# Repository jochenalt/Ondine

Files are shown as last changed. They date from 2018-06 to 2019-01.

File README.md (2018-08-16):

# Ondine
Ondine is a lovely ballet of robots. Right in the middle of development. Check the [Documentation](http://ondine.readthedocs.io). Contact me via the [hackaday page](https://hackaday.io/post/53678).

work in progress

### Contents
    /cad 	    CAD designs in Inventor 2018
    /theory     mainly on kinematics
    /code       source code (mainly C++)
    /schematics schematics in EAGLE 
    /docs		source of Ondine's [Documentation](https://http://ondine.readthedocs.io)
    /datasheets datasheets of components Ondine is made of

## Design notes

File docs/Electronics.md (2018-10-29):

# Electronics

Electronics takes care of the following topics

* <b>Control of the three brushless motors</b>. Brushless motoros require more control and electronics than brushed motors. Since industrial controlers are quite expensive, I did my own based on the [L6234 three phase motor driver](https://www.st.com/content/ccc/resource/technical/document/application_note/78/44/47/d5/a8/63/4a/8e/CD00004062.pdf/files/CD00004062.pdf/jcr:content/translations/en.C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), which is kind of outdated, but still has nice specs.
* <b>Running Kinematics and state control</b>. Kinematics and state control need to run with a high frequency and reasonable precision. I went with a [Teensy 3.5](https://www.pjrc.com/store/teensy35.html) ARM controller with 120MHz providing floating point arithmetics in hardware.
* <b>Communicate with the outside world</b>. The bot communicates via a small webserver connected to a local Wifi using the popular [ESP8266](https://www.seeedstudio.com/NodeMCU-v2-Lua-based-ESP8266-development-kit-p-2415.html) device.

# Control of a Brushless Motor

A brushless motor is driven by a magnetic field that turns 90° in advance of the motor's rotor. The diagram shows how this works in general.

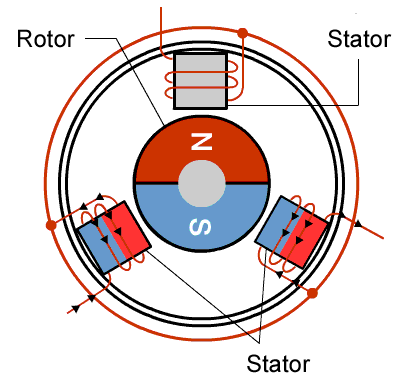
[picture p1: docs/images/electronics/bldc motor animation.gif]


But, the magnetic field turns in jumps of 120° which leads to high vibrations and jerky rotation especially when working at low speed. To improve that, the magnetic field has to turn continuously, which we can achieve by applying three sin waves modulated by PWM to each stator resulting in a smoothly turning magnetic field.

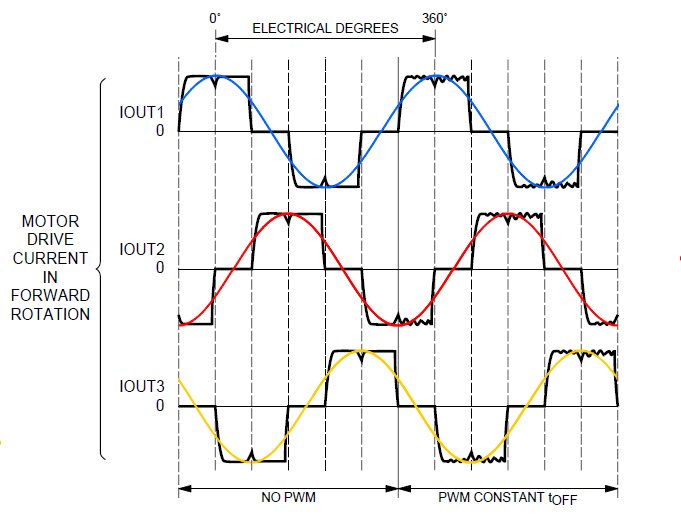
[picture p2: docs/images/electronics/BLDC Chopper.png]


To improve the ripple of the movement, space vector PWM (SVPM) can be used instead of plain PWM modulating sine waves. This is kind of electrical engineering black magic, an introduction can be found [here](https://www.switchcraft.org/learning/2017/3/15/space-vector-pwm-intro), frankly I did not spend the effort to dig into it, since it is so easy to implement and gains you a smoother movement.

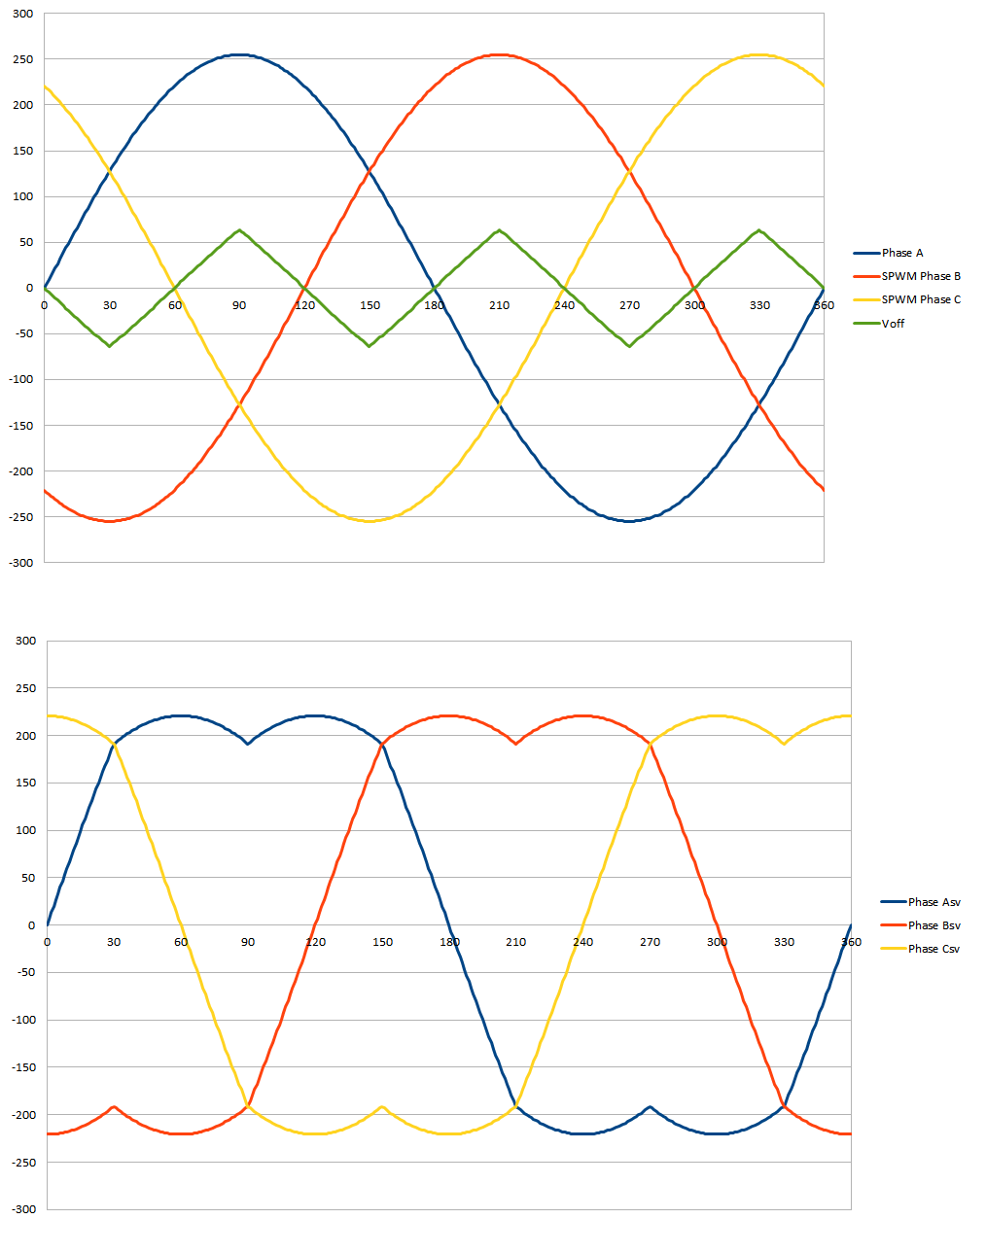
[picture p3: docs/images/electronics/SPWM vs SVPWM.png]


Computation is done by 





The motor driver L6234 has three PWM inputs, which need to be fed with svpm(t), svpwm (t + 120°), and svpwm(t + 240°). 

## Initial Calibration

The initial position of the rotor has to be considered in order to drive the magnetic field 90° ahead of the rotor's positon. For this purpose, I use an optical encoder with a startup procedure identifying the initial angle of the rotor (later on, it came to my mind that an absolute magnetic encoder could do this without the startup procedure. But it was too late).

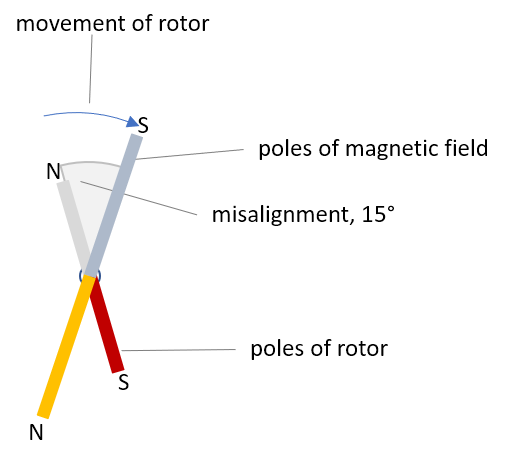
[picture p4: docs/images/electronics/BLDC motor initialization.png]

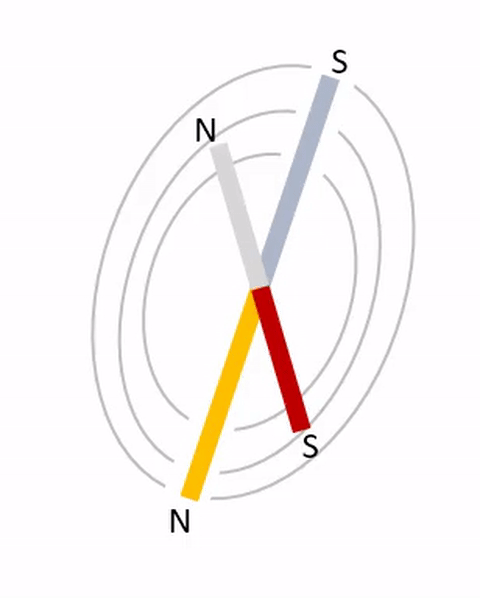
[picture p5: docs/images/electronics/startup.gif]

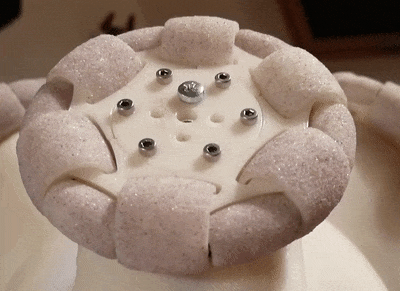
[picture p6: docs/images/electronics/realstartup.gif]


After the initialization procedure we know the current angle of the rotor. It is used later on to turn the magnetic field 90° ahead of the rotor. When we switch on the motor, we start with a very little amount of torque. The torque is slowly increased until the encoder recognized a movement. This happens after approx 0.3° (I have 1024 CPR encoders). The direction of the movement indicates the direction of the rotor's position relatively to the magnetic field. Now the magnetic field is turned torwards the rotor until the rotor has reached its starting position. We slightly increase the torque and start again waiting for a small movement which is then compensatd by turning the magnetic field. We repeat that until the magnetic field is perfectly aligned with the rotor while applying maximum torque. 

By this procdure, the magnetic files turns towards the current position of the rotor with increasing verve. It takes approx. 1s and is recognizable by a very small and short osccillation when starting up.

The advance angle of 90 degrees implies an issue when doing position control: If the motor is supposed to stick at one position and there's varying torque, the advance angle jumps from +90° to -90° everytime the control algrithm changes its direction. To avoid that jump, the PID controller's output is smoothed by a sigmoid function:



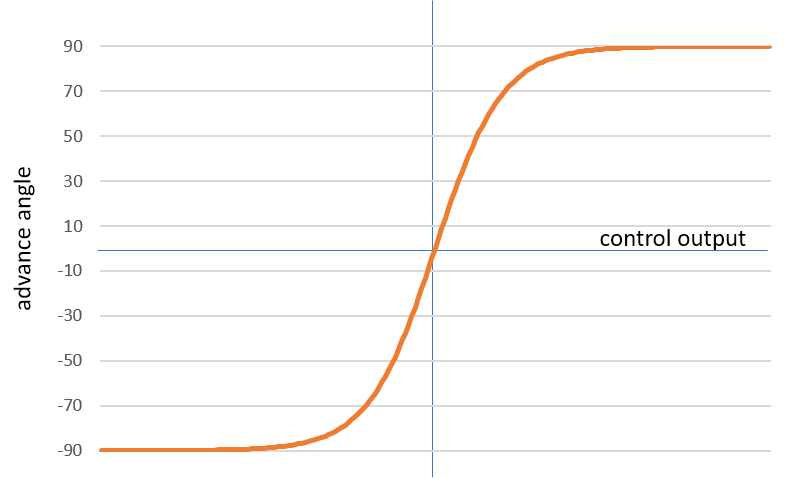
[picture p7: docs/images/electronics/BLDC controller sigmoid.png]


## PID Controller

Speaking of the PID controller of a brushless motor : I played around with a couple of controllertypes, I even implemented one of these fancy fuzzy controllers. Did not work out well, actually I got the impression that fuzzy controllers are kind of an academic hype only. I ended up with a plain gain-scheduled PID controller, i.e. a PID controller that has two sets of PID values: One for balancing, one for maximum speed. The input speed is used to identify the gains by interpolation between these two configuration sets.

All this is implemented in [BrushlessMotorDriver.cpp](https://github.com/jochenalt/Ondine/blob/master/code/BotController/BrushlessMotorDriver.cpp).

# Communication

The device should communicate with the outside world. A fully fledged SOC board (Raspberry or ODroid) seemed to be an overkill, so I used a small web module that became famous a couple of years ago. The [ESP8266](https://www.seeedstudio.com/NodeMCU-v2-Lua-based-ESP8266-development-kit-p-2415.html) can be programmed in C++ in an Eclipse IDE and already has a library implementing a webserver. Those weired scripting languages that always come with a device like that (in this case "LUA"), is nothing I wanted to spend time with.



# Microcontroller

The microcontroller should run the state control to make the bot balance and move, it has to control the motor drivers which uses up some capacity, and it has to receive commands coming from the webserver module. An Avr uC would be too much of a tuning pain, a fully fledged Linux board would be overengineered, so I went with my favrourite controller, a [Teensy 3.5](https://www.pjrc.com/store/teensy35.html) that has a 32bit-Arm M4 controller with enough memory, 120MHz, 5V compatibility, and a 32-bit FPU which comes in handy for kinematics and state control.



# Schematics 

The motors pull 2A max, so I choose the [L6234](https://www.st.com/content/ccc/resource/technical/document/application_note/78/44/47/d5/a8/63/4a/8e/CD00004062.pdf/files/CD00004062.pdf/jcr:content/translations/en.C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) to avoid soldering 18 MOSFETs. Luckily, there's a nice breakout from [Drotek](https://drotek.com/shop/en/home/212-brushless-gimbal-controller-l6234.html) that is convinient to use.

[](https://drotek.com/shop/505-large_default/brushless-gimbal-controller-l6234.jpg)

On the IMU side I went with the cheap and reliable MPU9250 on a drotek breakout

[](https://drotek.com/shop/en/imu/421-mpu9250-gyro-accelerometer-magnetometer.html)

There's not a big deal in the schematics, pretty standard I would say. There's a power supply with a switching 7805 (D3) (a normal power regulator would have required a heatsink for which I dont have enough space on the PCB). A relay REL1 turns on the power to the motors indiated by LED1, since I wanted to avoid issues during startup when the motors are not yet controlled by the uC but the drivers get power already. The Teensy uC is in the middle, its PWM pins go to the L6234 drivers, which output lines go to the motor sockets. To protect the uC, the PWM lines are connected with a resistor and z-diode limiting the voltage that is induced by the motors and might come back to the uC (I did that not as a precaution but as a learning point after I bricked a uC. The L6234 has the issue that there is an inner connection from the motor output to the incoming pwm pin, if it is not controlled correctly).

The optical encoders are connected to interrupt-able GPIOs of the uC (luckily, all Teensy GPIOs are interruptable). The ESP8266 breakout's D2/D1 is connected to the uC's  I2C-0 port, the logging output coming from the uC via UART5 is fetched by the ESP8266 via its half (only RX) serial port. The IMU MPU9250 is connected to the uC's I2C-1 port. Since the teensy is full of ports, there's no need to cope with the hazzle of multiple slaves on the same I2C bus. 

The S1 dip switch can be set to identify the board. The pololu motor driver U$1 is a used to control the brushed and encoded motor that lifts the enclosure from the ground.  

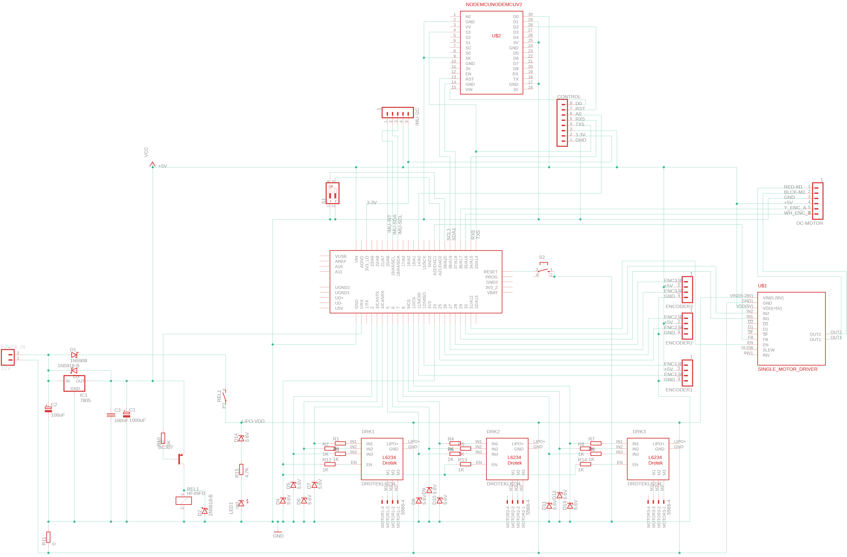
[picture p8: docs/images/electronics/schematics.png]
[](https://raw.githubusercontent.com/jochenalt/Ondine/master/docs/images/electronics/schematics.png)
(click to enlarge)

In the end, all parts fit into a standard 100x80 board

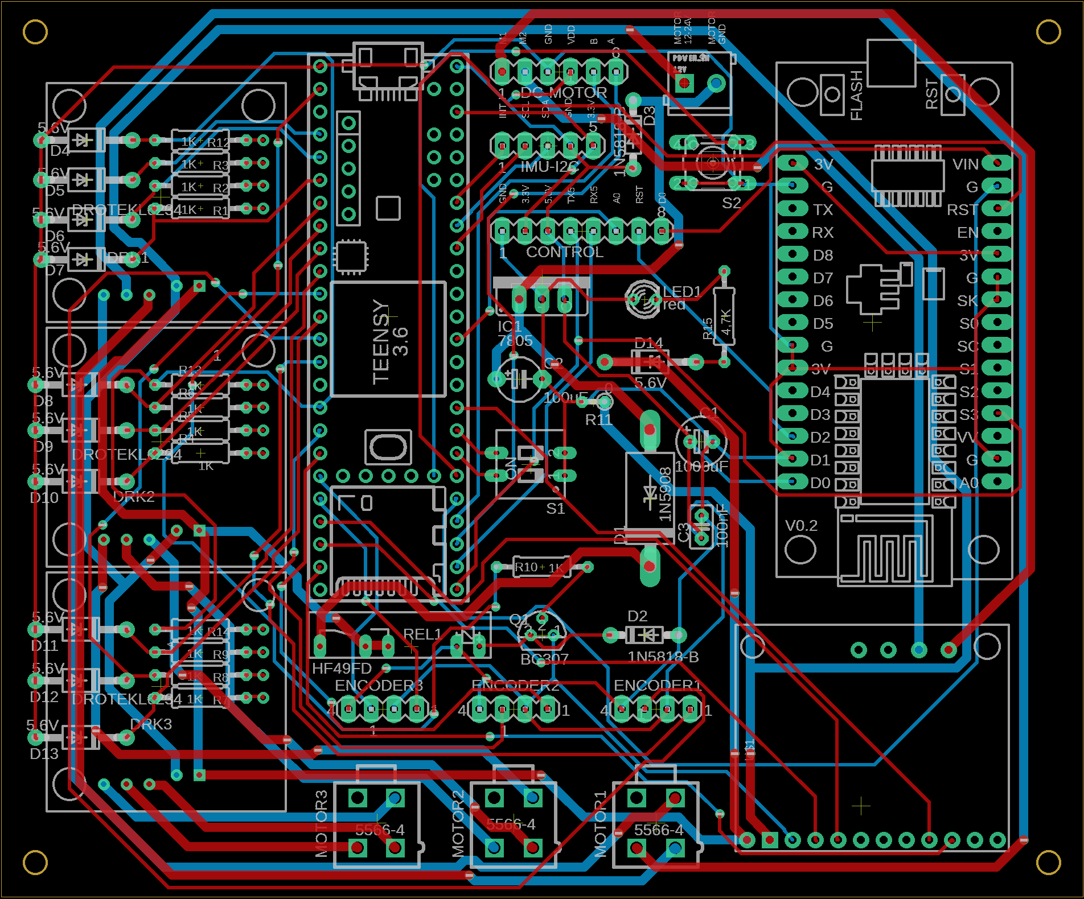
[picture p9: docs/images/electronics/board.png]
[](https://raw.githubusercontent.com/jochenalt/Ondine/master/docs/images/electronics/board.png)
(click to enlare)

Schematics and board in Eagle format is [here](https://github.com/jochenalt/Ondine/blob/master/schematics).

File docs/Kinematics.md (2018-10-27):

# Kinematics

Kinematics means to compute the speed of each wheel out of the body's movement and vice versa.
I will not bother you with the details of two weekend’s work, but make this story short, the final formula is:



which gives you the speed of every omniwheel out of the speed in x/y direction and the angular speed around the z-axis.
The system-specific variables used are

| Symbol | Description | Value |
|--- |---|--- |
| θ | angle between horizontal plane and the omniwheels directions [rad] | 45° = π/4 |
| r<sub>w</sub> | radius of the omniwheel in [mm] | 35mm |
| r<sub>b</sub> | radius of the ball in [mm] | 180mm |

The kinematic parameters are 

| Symbol | Description | 
|--- |---|
| ω<sub>wi</sub>| angular velocity of the i<sup>th</sup> wheel in [revolutions/second] |
| v<sub>x</sub> | body speed in x-direction in [mm/s]							 |
| v<sub>y</sub> | body speed in y-direction in [mm/s]							 |

In the formula above, <i>R</i> is the rotation matrix of the current tilt of the bot, it is a regular rotation matrix 



with <br>
φ<sub>y</sub> tilt angle of the bot in y direction in [rad]<br>	
φ<sub>x</sub> tilt angle of the bot in x direction in [rad]

For forward kinematics we need the formula reversed, which is



This gives you the speed in x and y direction out of the speed of all omniwheels

## Coordinate system

For kinematics, IMU and balance control, this coordinate system as seens from the top is used:

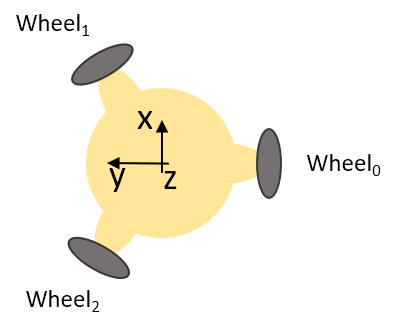
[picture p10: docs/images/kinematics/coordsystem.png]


## Implementation

During setup of the bot, we can precompute the so-called construction matrix <i>CM</i>.



During runtime within a continously loop, we need to apply the formula above with the precomputed construction matrix. Luckily, the tilt correction matrix <i>R</i> does not need to be multiplied completely with the construction matrix, since we have the sparse matrix



that reduces the amount of necessary multiplications drastically. Instead of the full matrix multiplication of <i>CM*R</i> with 81 floating point operations,  we can omit the cells where the sparse matrix is zero and would null out the result anyhow. By this, we need 10 out of 81 possible multiplications only.

All this is implemented in [Kinematics.cpp](https://github.com/jochenalt/ondine/tree/master/code/BotController/Kinematics.cpp)

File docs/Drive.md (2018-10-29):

# Drive Chain

Driving Omniwheels requires precise control, particularly when the bot is not moving. During balancing all motors move around the same position with many changes in directon. A regular drive with a geared brushed motor has a certain amount of backlash. Small corrections of the bot's position won't have an impact until the motor overcomes the backlash. Therefore, the controller will always overshoot allowing a smaller gain only. Therefore, it is essential to have a small backlash in the motor/drive combination.

# Torque, Power, and Gearbox Ratio 
I estimated the bot's weight approx. 3kg (=29N). A maximum tilt angle around 15° gives a force of 7N to be delivered by the drive. Ignoring the fact that a wheel's axis is not always perpendicular to the direction, and having wheels with a radius of 35mm results in a torque provided by one wheel of 7N*35mm = 0.025Nm. Motors typically provide 3000 RPM, the Bot's to-be speed should be 1m/s, so a wheel has a maximum speed of 2.4 rev/s. This gives a gearbox ratio of 1:20 max. I choose a gearbox ratio of 1:9. So, the motors torque should be 0.002Nm at 1500 RPM.
When I started looking for motors, I was lucky and made a snip on ebay, so all the computations above were useless. Anyhow, I got these wonderfull brushless [40W Maxon motors](https://www.maxonmotor.com/maxon/view/product/272768) for 5€ each

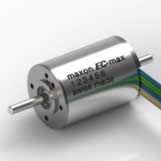
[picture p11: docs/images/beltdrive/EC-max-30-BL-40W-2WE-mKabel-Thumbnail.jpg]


# Failed Gearboxes
The quality of these motors were setting the scene, the gearbox had to be close to this. A gearbox from maxon was no option (starts at 150€), and I had the ambition to build something without backlash. So, I tried a [harmonic drive with timing belts](https://hackaday.io/project/19405-strain-wave-gear-with-timing-belts) based on Simon Merrets ideas, and I had a go with a cycloid drive due to its mechanical beauty. Both suffered from the same deficiency: The parts were 3D-printed with a precision of 0.2mm at best, which is not sufficient to get a proper efficiency. Boths gears were groaning loudly and had a significant inner friction. The motor had to supply a significant amount of power to overcome this friction and started moving with a small jerk.

Next try was a planetary box which turned out to be acceptable. Play was low, required space was ok as well:



But, after reducing the distance between the gears to minimize the play, the gearbox started to produce an annoying plastic sound even after adding a heringbone gearing, so I dismissed this as well.

# Final Gearbox 
Last and successful try was the most boring gear type: timing belts. Still, the advantages were convincing: Low play by nature, silent, and cheap. Only issue is the space required. But this could be mitigated by a design which outer dimensions is dominated by the wheels only not wasting too much space with hubs or flanges etc:

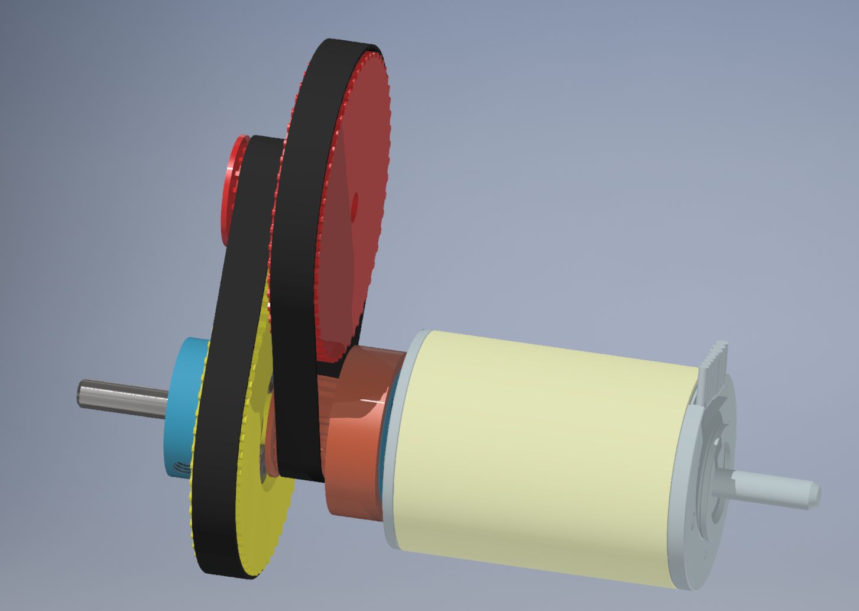
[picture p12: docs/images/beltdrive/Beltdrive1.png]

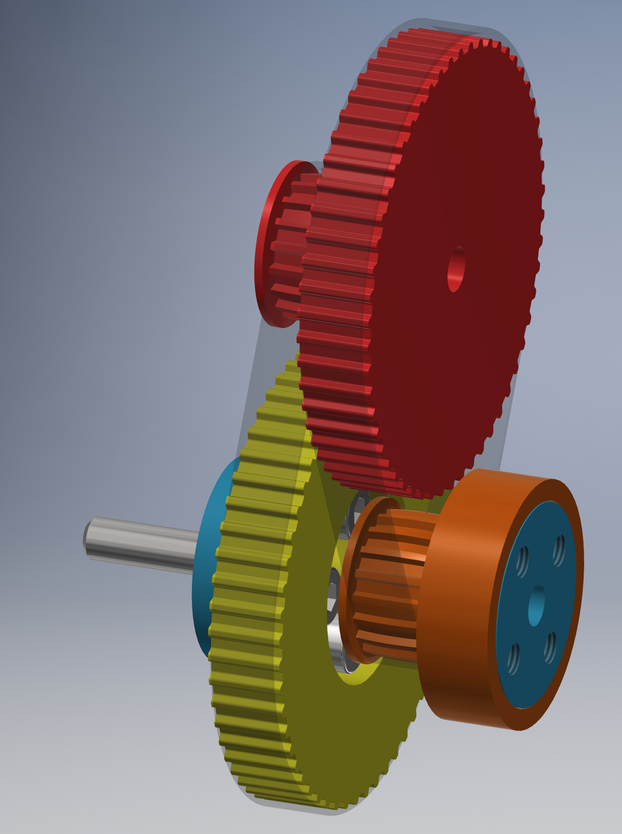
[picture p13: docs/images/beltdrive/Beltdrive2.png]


In total the belt drive is embedded into the enclosure like this

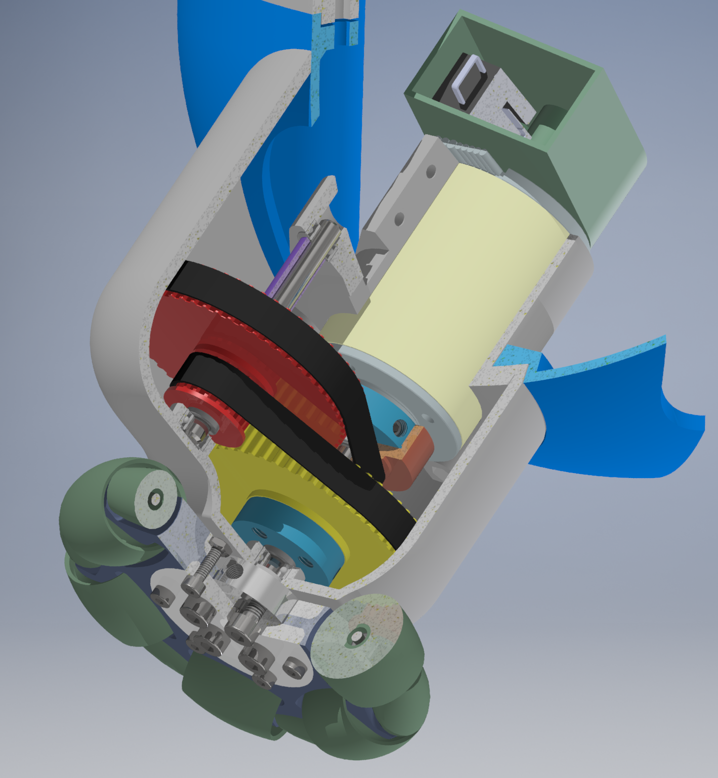
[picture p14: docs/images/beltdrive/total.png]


Especially the bearing of the output axis inside the pinion at the motor made this thing compact:

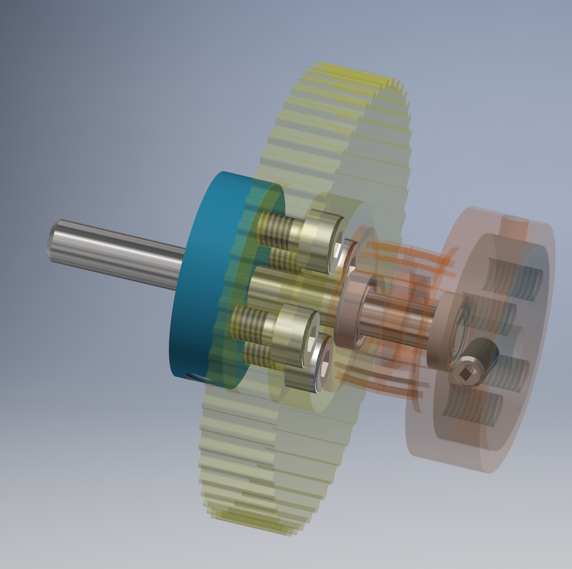
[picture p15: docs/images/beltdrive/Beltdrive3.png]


In the first try the timing belts touched the verge of the pinions resulting in an awful squeaking, until I gave the pinion's teeth a round profile that centred the timing belt in the middle of the teeth.  In order to not have remains of suport material coming from the 3D printing process, I cut the pinion's CAD model by half, and glued it after printing. It can be  seen on the original parts (the fine line in the middle of the pinion)

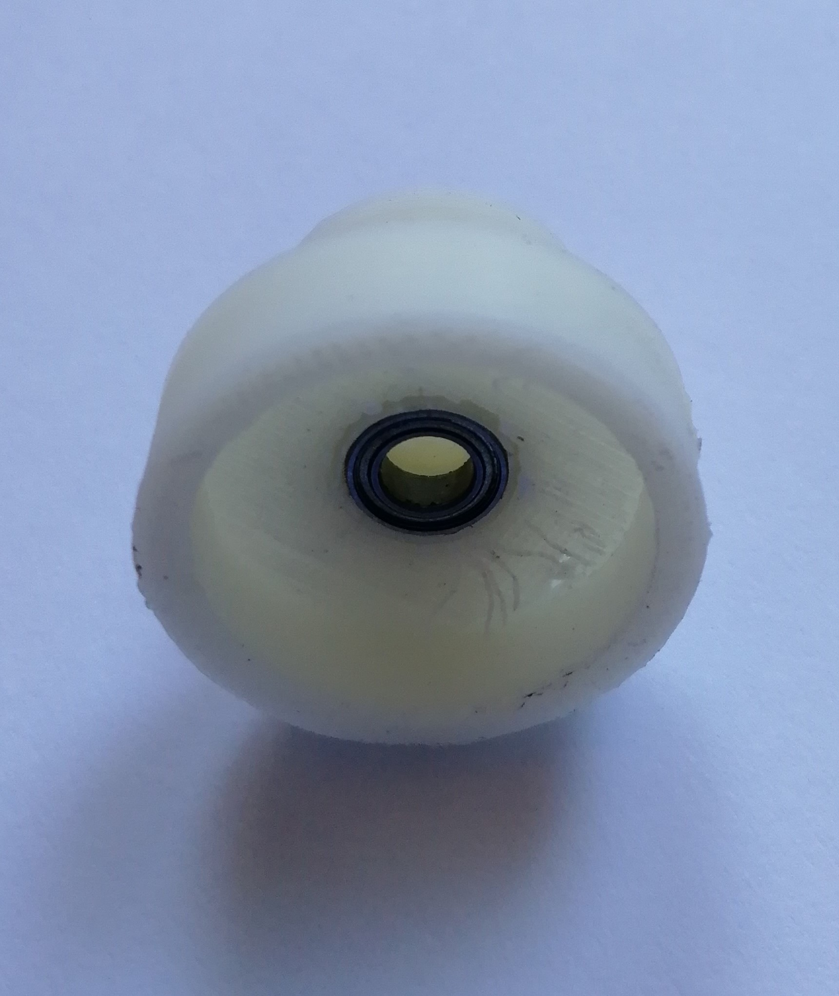
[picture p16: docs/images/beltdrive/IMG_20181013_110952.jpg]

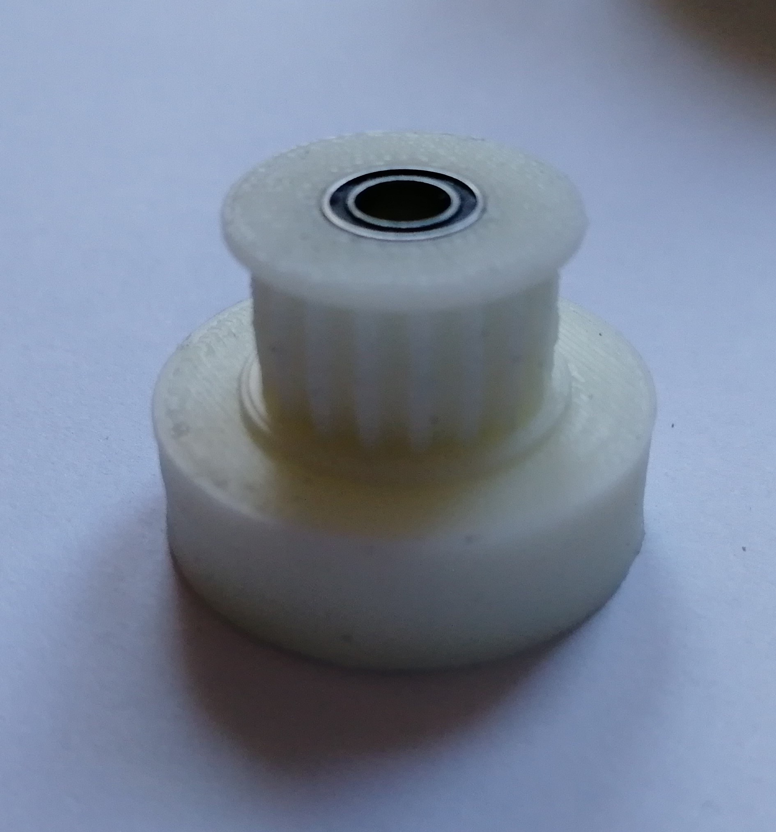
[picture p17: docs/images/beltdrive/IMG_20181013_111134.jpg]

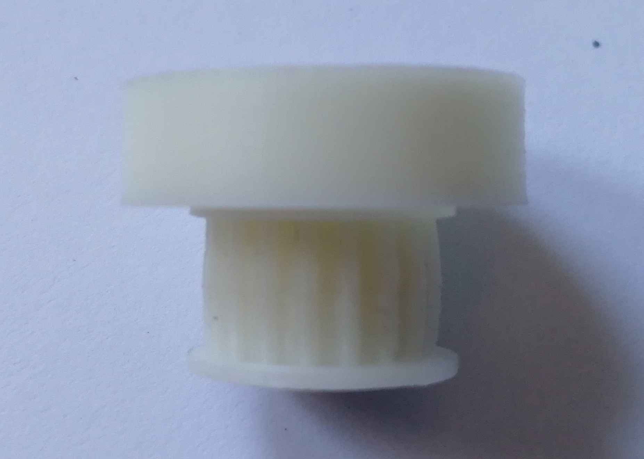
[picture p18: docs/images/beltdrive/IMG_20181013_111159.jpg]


The big wheel has bushings on both sides of the axis

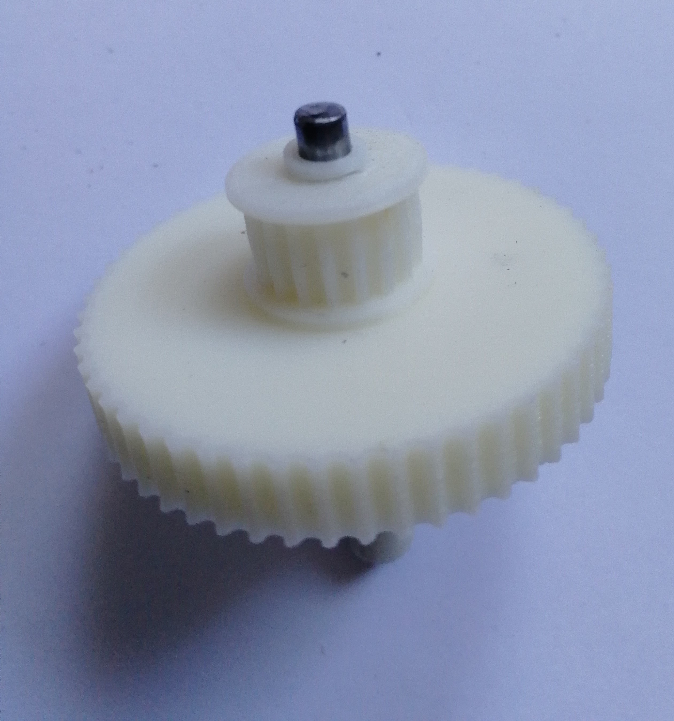
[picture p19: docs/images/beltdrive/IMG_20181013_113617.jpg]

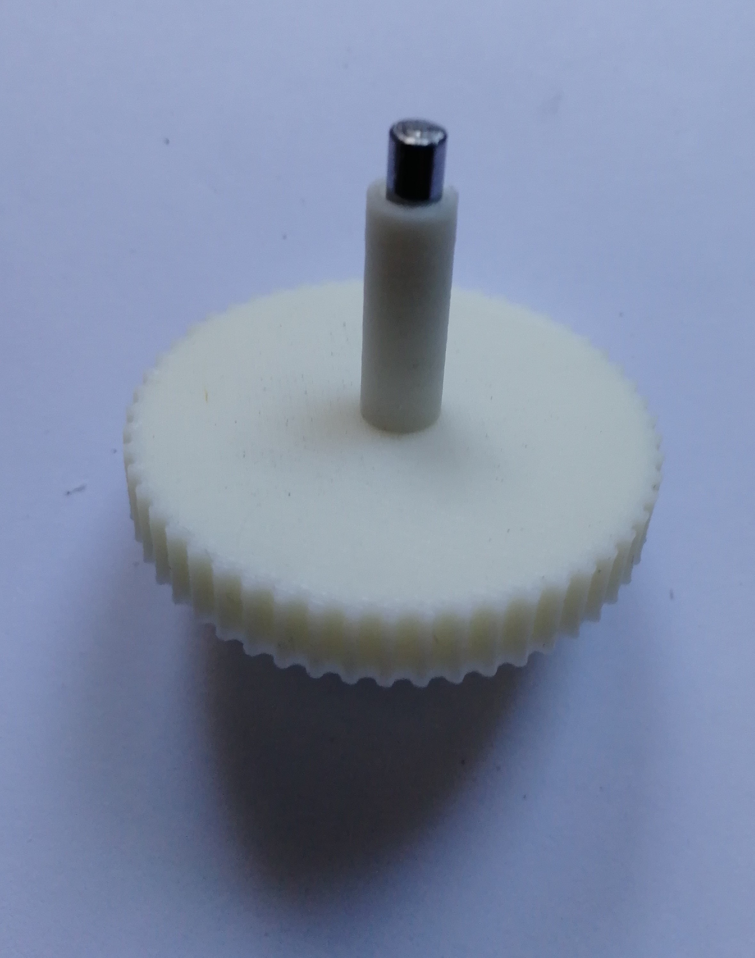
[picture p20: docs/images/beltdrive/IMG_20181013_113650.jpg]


The output wheel incorporates a mounting hub to connect the wheel and the axis 

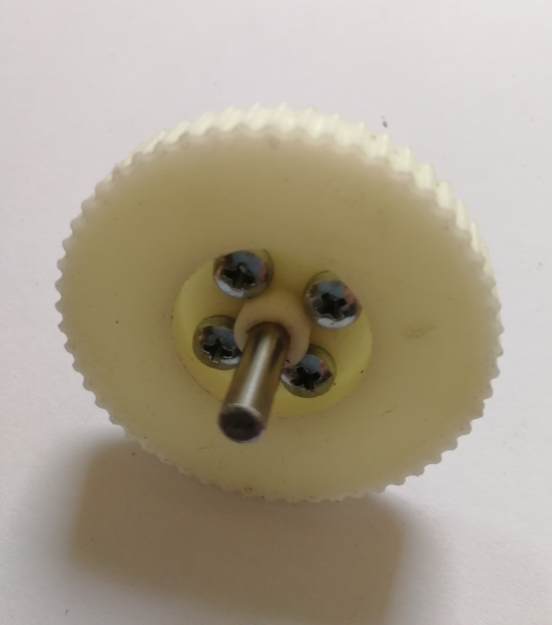
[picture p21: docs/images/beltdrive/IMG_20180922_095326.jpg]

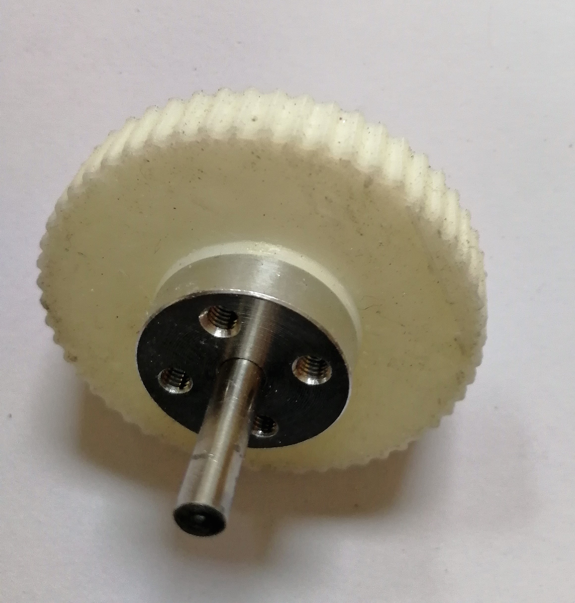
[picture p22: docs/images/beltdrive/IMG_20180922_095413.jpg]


Assembly starts with the enclosure and the output wheel. The three threaded rods that look out of the enclosure are hex head screws I glued into the enclosure to prevent them falling into the enclosure.

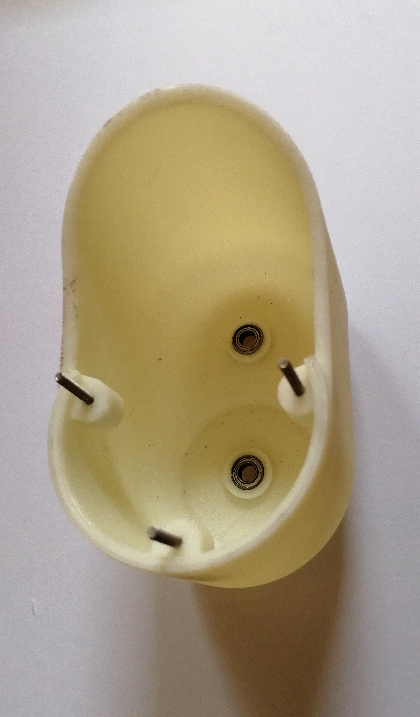
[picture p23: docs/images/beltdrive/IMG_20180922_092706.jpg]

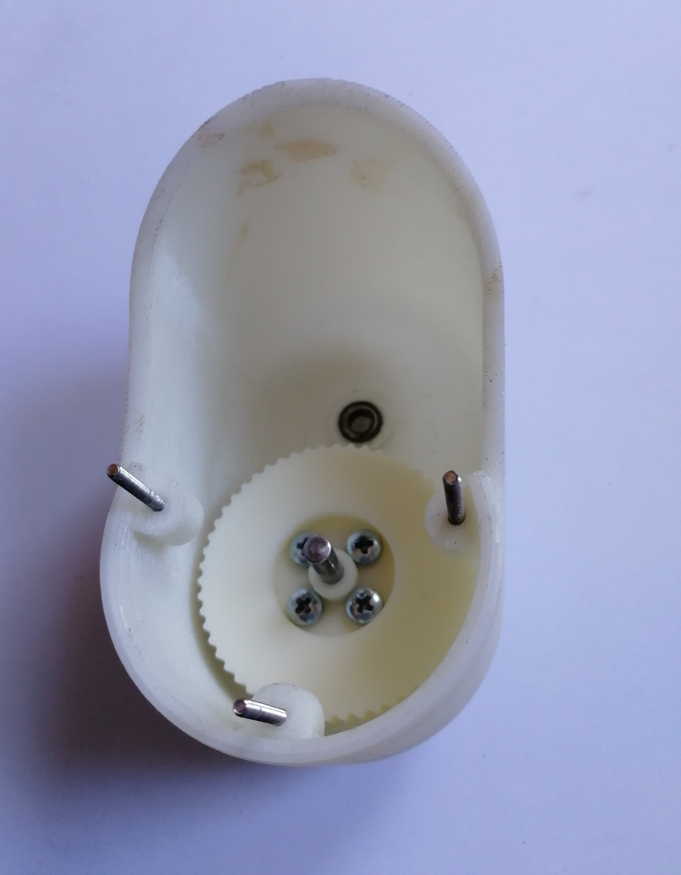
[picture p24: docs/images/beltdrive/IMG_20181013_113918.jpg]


Then the big wheel and the output timing belt is added (the stains on top of the enclosure is my blood)



The pinion and the motor is assembled like this. 



And in a tricky operation the motor is moved into the enclosure, keeping the second timing belt at the right position



Finally it looks like this (without encoder)



Now, the motor needs to be pushed into the enclosure until the output axis has no axial play anymore. Then, the motor can be screwed in its enclosure.



This is done three times. Then, the drive chains are screwd to the bottom part of the bot 



and it is really moving!



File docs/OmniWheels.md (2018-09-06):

# Omniwheels

The omniwheel I was looking for should follow the idea of the [japanese patent 2001-191704](https://astamuse.com/ja/published/JP/No/2001191704) from 2001. For your convinience, [this](https://translate.google.com/translate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) is the google translation of it.



This patent has a surprising design of the big roll. Its width is much smaller than the small rolls, and it runs with one bearing only. I was not able to find out why the authors chose a design so complex to manufacture. 



My [CAD model](https://github.com/jochenalt/Ondine/blob/master/CAD/OmniWheel.iam) needs to be 3d-printed, and the spoke of the patent is so thin, that this would never work. It  carries the bot's full weight, so it requires more material on the spots where the bearings are mounted. So, I designed the spoke with a constant distant to the roll giving the spoke a round surface where it faces the roll.

I ended up with that design, that has an identical width of all rolls and two bearings each. 




Still, I was scared that a bot of 3kg could be too heavy for the spoke, so I tried a stress analysis with a target acceleration of 1.0 m/s<sup>2</sup> resulting in a wheel torque of 0.04Nm (roughly). The weak point of the spoke is suprisingly not the marked thin part. The simulated weight of the bot seems to be much more significant than the torque applied. Finally, ABS seems to be strong enough to carry the bot.



As a courtesy to the japanese patent, I arranged the 3D-printed parts in beautiful manner:



The first assembly is necessary to check the tolerances. The slightest amount of warping during printing would make the rolls wobble; perfect rolls need to be selected in this phase.



Then I realized, that the friction of ABS rolls on a ball made of rubber or something was quite poor. There's little you can do about the 3d printed material, so I needed some kind of cover. I was thinking of rubber spray, but found out, that sand paper has a perfect friction on rubber. So, I looked for a material similar to sand paper and found corundum, which is sand with sharp edges. Originally it is used for blasting, so it is quite cheap to get. Thing is, that you can  order it in quantities of at least 5kg only. The remaining 4,95kg can be put in the garden to attract and fool ants.

To adhere corundum to the rolls I used 2-component epoxy glue. It is a messy experience to coat small rolls with glue and rolling them in a can of corundum sand.



To improve the quality of the adhesive layer, you can add instant adhesive with low viscosity (intended for porose surfaces) on the rolls. This is the way industrial sandpaper is manufactured to support a grain at its flanks. The final wheel looks really nice:



The CAD files can be found [here](https://github.com/jochenalt/ondine/tree/master/CAD/OmniWheel.iam).

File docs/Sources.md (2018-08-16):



## Download Links

* [CAD Models](https://github.com/jochenalt/Walter/tree/master/cad)
Designs made with TurboCAD, used to 3D-print all parts
* [Schematics](https://github.com/jochenalt/Walter/tree/master/schematics)
Cortex and Power Supply PCB made with KiCAD
* [Source Code](https://github.com/jochenalt/Walter/tree/master/code)
C++ code of Cortex, Trajectory Planner, and Webserver  
* [Datasheets](https://github.com/jochenalt/Walter/tree/master/datasheets)
Datasheets of components Walter is made of
* [Zip](https://github.com/jochenalt/Walter/archive/master.zip)
Give me everything

## Contact 

Please contact me via my [hackaday](https://hackaday.io/project/19968-walter) page.

## FAQ

### 3D print
I used the Zortrax M200 printer with Z-ultrat, a high-temperature ABS. For all parts besides plugs and belt spanners and gears I applied the  parameters 0,14mm resolution, 4 layers wall thickness and 15% infill. For the latter, I used 50% infill. All in all, Walter required ca. 2kg filament.

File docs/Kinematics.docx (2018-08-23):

Kinematics means to compute the speed of each wheel out of the bots movement and vice versa.

I wont bother you with the details oft wo weekend’s work. To make a long story short, the final formula is:

[ω_(w1) ω_(w2) ω_(w3) ]=-1/(r_w) (0, cosθ, -sinθ-(√3)/2 cosθ, -(cosθ)/2, -sinθ(√3)/2 cosθ, -(cosθ)/2, -sinθ)R^T (0, -1, 01, 0, 00, 0, -r_b )[v_x v_y ω_(bz) ]

which gives you the speed of every omniwheel out of the speed in x/y direction and the angular speed around the z-axis.

The system-specific variables used are

θ | angle between horizontal plane and the omniwheels directions [rad] | 45° = π/4
r_w | radius of the omniwheel in [mm] | 35mm
r_b | radius of the ball in [mm] | 180mm

The kinematic parameters are

ω_(wi) | angular velocity of the i.th wheel = [(revolutions)/(second)]
v_x | speed in x-direction in [(mm)/(second)]
v_y | speed in y-direction in [(mm)/(second)]

In the formula above, R is the rotation matrix of the current tilt of the bot, it is a regular rotation matrix

R_x *R_y =[1, 0, 00, cosφ_x , -sinφ_x 0, sinφ_x , cosφ_x ] [cosφ_y , 0, sinφ_y 0, 1, 0- sinφ_y , 0, cosφ_y ]= [cosφ_y , 0, sinφ_y sinφ_x sinφ_y , cosφ_x , -sinφ_x cosφ_y -cosφ_x sinφ_y , sinφ_x , cosφ_x cosφ_y ]

where

φ_y | tilt angle of the bot in y direction in [rad]
φ_x | tilt angle of the bot in x direction in [rad]

For forward kinematics we need the formula reversed, which is

(0, -1, 01, 0, 00, 0, -r_b )^(-1) *R^() (0, cosθ, -sinθ-(√3)/2 cosθ, -(cosθ)/2, -sinθ(√3)/2 cosθ, -(cosθ)/2, -sinθ)^(-1) [ω_(w1) ω_(w2) ω_(w3) ](-r_w )= [v_x v_y ω_(bz) ]

This gives you the speed in x and y direction out oft he speed of all omniwheels

Implementation

During setup of the bot, we can precompute the so-called construction matrix CM.

CM= 1/(r_w) (0, cosθ, -sinθ-(√3)/2 cosθ, -(cosθ)/2, -sinθ(√3)/2 cosθ, -(cosθ)/2, -sinθ)

During runtime a continously running loop, we have the tilt angles coming from the IMU, and compute the tilt correction matrix R. We are lucky that al that is finally multiplied with the sparse matrix

(0, -1, 01, 0, 00, 0, -r_b )

which means that we do not have to compute a full matrix multiplication of CM*R with 81 floating point multiplications, but can omit the computation where the matrix above has a 0 requiring 10 multiplications only.

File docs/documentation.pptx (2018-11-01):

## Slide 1

Wheel1

movement of rotor

S

N

N

S

x

N

S

poles of magnetic field

y

z

Wheel0

misalignment, 15°

Wheel2

poles of rotor

N

S

S

N

N

S

advance angle

control output

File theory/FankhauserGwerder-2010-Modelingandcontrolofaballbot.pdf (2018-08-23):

See discussions, stats, and author profiles for this publication at: https://www.researchgate.net/publication/259602161
Modeling and Control of a Ballbot (https://www.researchgate.net/publication/259602161_Modeling_and_Control_of_a_Ballbot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)

Thesis · June 2010

CITATIONS
26

READS
1,241

### 2 authors, including:

Some of the authors of this publication are also working on these related projects:

ANYmal Research View project (https://www.researchgate.net/project/ANYmal-Research?el=1_x_9&_esc=publicationCoverPdf)

Péter Fankhauser (https://www.researchgate.net/profile/Peter_Fankhauser2?el=1_x_5&_esc=publicationCoverPdf)
ETH Zurich (https://www.researchgate.net/institution/ETH_Zurich?el=1_x_6&_esc=publicationCoverPdf)

### 40 PUBLICATIONS 337 CITATIONS

SEE PROFILE (https://www.researchgate.net/profile/Peter_Fankhauser2?el=1_x_7&_esc=publicationCoverPdf)

All content following this page was uploaded by Péter Fankhauser (https://www.researchgate.net/profile/Peter_Fankhauser2?el=1_x_10&_esc=publicationCoverPdf) on 08 January 2014.

The user has requested enhancement of the downloaded file.

## Bachelor Thesis

Spring Term 2010; Authors; Péter Fankhauser Corsin Gwerder

Autonomous Systems Lab
Prof. Dr. Roland Siegwart

Modeling and Control of a Ballbot

Supervisors
Stefan Leutenegger
Dr. Francis Colas

## Abstract

A ballbot is an extremely agile mobile system due to its natural instability. In order to perform complex motions at high speeds, a sophisticated controller is needed. This thesis first approximates the dynamics of a ballbot with three two-dimensional decoupled systems. It analyzes the dynamic internal forces occurring when operating a ballbot. Conversions for torques, moments of inertia and the odometry are calculated for the implementation of a controller in the real system. The planar decomposition is the state of the art approach for ballbot control. However, it mainly suffers from unphysical modeling of actuators requiring artificial calculations, and neglecting the strong coupling effects that are important for dynamic motion. To overcome these limitations, a full three-dimensional model is proposed. This new model is verified and the advantages are shown by comparing it to the planar model. The performance of a linear quadratic controller is simulated in real-time with MATLAB and displayed in a three-dimensional visualization. As a consequence of the strong nonlinearities, a controller based on gain scheduling shows to improve the performance significantly. With the resulting controller, the prototype is able to follow highly dynamic, complex trajectories, which is shown in various experiments. Compared to previous solutions, this fundamentally new approach to control a ballbot allows for a considerably higher performance regarding acceleration, speed, motion precision and robustness.

I

II

## Acknowledgements

We would like to thank a number of people who have encouraged and helped us in writing this thesis. We are very proud of the achieved results and we appreciate the support we received from all sides.

We are much obliged to Prof. Dr. Roland Y. Siegwart for his support and confidence in our team and for providing the opportunity to be part of such a far reaching project.

Special thanks to our supervisor and PhD student Stefan Leutenegger. His broad knowledge in system modeling and control and his very professional and friendly way of support had a wide influence on the results and also on our education. He persistently helped us with many complex questions and motivated us to extend the scope of the project into the right directions.

Many thanks to Dr. Francis Colas for the supervision of this thesis and also for coaching the whole focus project. Not only was he able to keep the very important overview, with a lot of effort and knowledge about each thesis, but also helped defining and managing all interconnections in order to bring all parts together.

We would like to thank Dr. Marcel Buttliger and Céline Martin for their extensive help with the structure and proofreading of this work.

We are very thankful to all members of Team Ballbot and are very happy to have spent a year working together in this project. We have formed a very capable team and helped each other to realize our ideas.

Most importantly, we are very grateful to all our friends and family members who sup-ported us during the whole project and helped us to achieve our aims.

Zürich in June 2010,
Péter Fankhauser and Corsin Gwerder

III

IV

## Contents

1 Introduction | 1
2 Planar System Modeling and Control | 5
3 Simulation and Verification of the Planar Model | 19

V

4 3D System Modeling and Control | 27
5 Simulation and Verification of the 3D Model | 41
6 Performance Analysis | 47
7 Implementation | 50

VI

8 Conclusion | 53
Bibliography | 55
A Schedule | 57
B Planar System Modeling | 58
C Conversions | 67
D Odometry | 74
E 3D System Modeling | 78
F Verification Plots | 85

VII

VIII

## Abbreviations

3D | Three Dimensional
ARM | Advanced RISC Machine
ASL | Autonomous Systems Lab
CAD | Computer Aided Design
CMU | Carnegie Mellon University
DC | Direct Current
DoF | Degrees of Freedom
EPOS | Positioning controller
ETH | Swiss Federal Institute of Technology
FIR | Finite Impulse Response
GUI | Graphical User Interface
IMU | Inertial Measurement Unit
LQR | Linear Quadratic Regulator
PD | Proportional–Derivative
PI | Proportional–Integral
PID | Proportional–Integral–Derivative
RISC | Reduced Instruction Set Computer
RS-232 | Recommended Standard 232
TGU | Tohoku Gakuin University
UA | University of Adelaide
ZHAW | Zurich University of Applied Sciences
ZHdK | Zurich University of the Arts

IX

X

Introduction

## 1 Introduction

### 1.1 Motivation

Figure 1.1: General concept of a ballbot

A ballbot uses a single ball as core of its propulsion system (fig. 1.1). Tilting spontaneously

in any direction and rotating about its own axis, a ballbot performs its motion in a very unique way. The concept is very similar to an inverted pendulum. Especially designed as an unstable system, the fundamental part of a ballbot is a reliable control.
Other ballbots have been developed (see 1.5), but none of them is able to utilize the full

potential of agility, which is a core feature of a ballbot. The prototype Rezero has been built with the goal of demonstrating an unprecedented level of agility and the capability of such a propulsion system.

### 1.2 Context

The presented thesis is closely linked to the ETH Focus Project Ballbot 2009/10 [11]. In

this project, eight undergraduate mechanical engineers from ETH Zurich, two electrical engineers studying at ZHAW¹

and three industrial design students from ZHdK² have developed a ballbot named Rezero³ within nine months. The goal of this project was to

develop a fully operational prototype of a ballbot which is unique in its motion, dynamics

1Zurich University of Applied Sciences
2Zurich University of the Arts
3The name Rezero refers to the important relationship between the real part of the poles π of the transfer function and zero: a system with Re(π) > 0 is unstable.

1.3 Goals | Introduction
| and agility compared to existing ballbots – a goal which can only be achieved with a
strong focus on modeling and control.

### 1.3 Goals

| This Bachelor thesis aims to analyze the system of the ballbot Rezero and to develop and
| implement an appropriate controller for it. The controller has to be optimized to ensure a
| highly dynamic and maneuverable motion of the ballbot. Additionally, a flexible realtime
| simulation of the system is required for early analysis and for the purpose of laying the
| foundation for other theses on the same prototype. The controller should comply with the
| conceptual requirements set forth by the Focus Project Ballbot as precisely as possible:
- different input modes (position, velocity, acceleration set points),
- speed up to 2 m/s,
- tilt angles up to 20◦
,
- high motion precision,
- high dynamic robustness.

Details are described in the project report ”

| Rezero – dynamisch stabil auf einer Kugel“ [11].

### 1.4 System Overview

## Battery

## Microcontroller Linux board

## Motors with gearhead Omniwheel

## Ball

## Power electronics

## IMU

## Encoder

## Ball arrester

Figure 1.2: System description of Rezero

The system ballbot shown in figure 1.2 is a dynamically stable robot balancing and driving on a single ball. It is composed of three main parts: the ball, the propulsion

Introduction | 1.5 State of the Art

system and the body, the latter carrying all the electronics. The propulsive subsystem
consists of three omniwheels⁴ driven by 200 W DC brushless motors with gear heads

with a maximum torque of 5 Nm. Each motor has an encoder attached, measuring the position and speed of the motor axis. The ball consists of a 2 mm thick aluminum hollow sphere, coated with a 4 mm high stiction synthetic. The ball arrester pushes the ball towards the omniwheels in order to increase the contact force.
A very important sensor is the inertial measurement unit (IMU) which measures all three Euler angles and the angular rates of the body. On the microcontroller, an ARM⁵ 7, the

controller is implemented running at 157.8 Hz. The set points are sent to the embedded microcontroller by a Linux board over RS-232.
A list of parameters is given in table 2.1 and details on all components are described in [11].

### 1.5 State of the Art

The first ballbot was developed in 2006 at Carnegie Mellon University (CMU) in the USA ([10],[12]). Another ballbot was developed at Tohoku Gakuin University (TGU) in Japan [7] and a third one as a student project 2009 at the University of Adelaide (UA) in Australia [5]. The specifications in table 1.1 show the differences.

University | CMU | TGU | UA
Year | 2006–2010 | 2006–2008 | 2009
Weight | 45 kg | 11 kg | 34.5 kg
Height | 150 cm | 50 cm | 160 cm
Maximum tilt angle | ◦ <5 <1 | ◦ <1 | ◦
Maximum speed | <0.1 m/s | <0.3 m/s | <0.1 m/s
Rotation around its own axis | (yes) | yes | no
Used controller | LQR/PID | PD | LQRI

Table 1.1: Specifications of already existing ballbots

The first version of the CMU ballbot was stabilized with a LQR (linear quadratic regulator) and an inner PI (proportional–integral) controller, the second version with a cascaded PID (proportional–integral–derivative) controller. The TGU ballbot uses a PD (proportional–derivative) controller. The UA ballbot is controlled with an LQR controller

that uses an additional integrating part. It is important to mention that all these projects developed a controller based on a planar model as is described in section 2.1.

4A holonomic wheel that can assign forces into to the tangential direction and allows low-friction motion into the lateral direction.
5Advanced RISC Machine

1.6 Project Schedule and Procedure | Introduction

### 1.6 Project Schedule and Procedure

The project described in this report is structured into chronological phases which end with the following milestones:

17.03.2010: Simulation environment is available to others

29.03.2010: Ballbot is balancing

12.04.2010: Ballbot is moving, state of the art

26.04.2010: Global system test 1

10.05.2010: Global system test 2

A detailed schedule is shown in the appendix A.
At the beginning of the project, the focus is set on the simulation, because other work within the focus project is heavily relying on it. The first system model is based on a planar simplification of the system. Based on the result of the simulation, the next step is to implement the controller and get the ballbot to keeping stability. With first tests, the controller is improved to reach the state of the art.
A new approach is taken by modeling the full three-dimensional system, allowing the design of a much better performing controller. With a test driven optimization, the controller is constantly improved and the results are verified in the global system tests 1 and 2.

### 1.7 Structure of the Report

The report is subdivided in seven major chapters. A first chapter describes the Planar System Modeling and Control (2), followed by the Simulation and Verification of the Planar System (3). The same structure is followed with the 3D System Modeling and Control (4) and the Simulation and Verification of the 3D System (5), representing the

chronological order of the development of the ballbot.
The results are discussed in Performance Analysis (6) and the details of the implementation process described in Implementation (7).

Planar System Modeling and Control

## 2 Planar System Modeling and Control

### 2.1 Model

### 2.1.1 Model Description


Figure 2.1: The three planar models, each model consists of the ball, the body and the actuating wheel

The three-dimensional system is divided into three independent planar models (fig: 2.1), where each can be described with the following two Degrees of Freedom (DoF):

- 1 DoF for the rotation/translation of the ball
- 1 DoF for the rotation of the body

The propulsion system, which is composed of three omniwheels, is modeled as one virtual actuating wheel in each plane which drives the ball. That particular wheel does of course not have the same position and speed as the omniwheels in the real system. Therefore, conversions are needed (see section 2.3).

2.1 Model | Planar System Modeling and Control
| The states of the system are the orientation angles and angle rates of the body and the
| position and speed of the ball. Since all these states are measured by the IMU and the
| motor encoders, the system outputs are equal to the states. The inputs are the torques
generated by the motors.

### 2.1.2 Assumptions

| In the planar system modeling, the system is treated as three independent planar models.
| Therefore no coupling effects between these three models are taken into account. Two
| of them (the ones in the xz- and yz-plane) are identical and very similar to an inverted
| pendulum, as shown on the left side of figure 2.2. The third one (in the xy-plane)
| describes the rotation around the z-axis in the body fixed reference frame, often described
| as the rotation around the ballbot’s own axis (right side of figure 2.2).
| The system is assumed to consist of three rigid bodies: the ball, the actuating wheel and
| the body. The three motors and omniwheels are therefore simplified as one actuating
wheel that fits in a plane.
Additionally, the following assumptions are made:
| No slip The contact points between the ball and the ground and between the wheels and
| the ball are assumed to be free of slippage. The system construction is optimized
| in order to minimize possible slipping. Thus, the torques applied have to be limited
| within the range that does not cause slippage in order to ensure the validity of the
model.
| No friction Even though friction occurs in the system, it is neglected except for the
| rotation of the ball on the ground around the z-axis, because this is the friction
| with the biggest impact. Non-continuous friction is hard to represent analytically
| and would generate equations much more complex than without friction. Also, the
precise measuring of friction is difficult.
| No deformation Because of its synthetic coating, deformation appears at the contact
| points of the ball. This has to be neglected in order to keep complexity at a
manageable level.
| Fast motor dynamics The power electronics control the dynamics of the motors much
| faster than the controller the dynamics of the stabilized system. Consequently, the
| motor torques are modeled to be the inputs of the system.
| Ball moves only horizontally In order to keep the prerequisite for the no slip condition,
| vertical movement of the ball has to be neglected. Finally, this model is designed
| to move primarily on flat surfaces without steep inclination.

Planar System Modeling and Control | 2.1 Model

## mA, ΘA

### rK sinα

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
ΘW,xy

ΘA,xy

Figure 2.2: Sketch of the planar models showing the coordinates and parameters. On the left side the model for the two vertical planes and on the right side the xy-plane model is shown.

### 2.1.3 Coordinates

To describe the system, the coordinates shown in figure 2.2 are used. ϑx,y,z represent the orientation of the body, ϕx,y,z represent the orientation of the ball and ψx,y,z are the angles of the virtual actuating wheels. Using the following minimal coordinates, the system can be completely described.

~qxy =

"
ϕz
ϑz
~qyz =

"
ϕx
ϑx
~qxz =

"
ϕy
ϑy
(2.1)

### 2.1.4 Binding Equations

All coordinates can be expressed as functions of the minimal coordinates, which is necessary in order to derive the equations of motion. The positions of the ball, the wheel and the body can be written as follows, using the rolling constraint¹
xK = ϕxrK | (2.2)
xW = ϕxrK + sin ϑx · (rK + rW ) | (2.3)
xA = ϕxrK + sin ϑx · l | (2.4)

Analogous relations are valid for the y coordinates.

1Meaning, that for example the balls position is determined by its slip free rolling on the ground.

2.1 Model | Planar System Modeling and Control

The rotation of the actuating wheel expressed as a function of the minimal coordinates yields the following equations.

ψ˙
x =

rK
rW
ϕẋ − ϑ˙
x
− ϑ˙
x | (2.5)

ψ˙
y =

rK
rW
ϕ˙ y − ϑ˙
y
− ϑ˙
y | (2.6)

ψ˙
z =

rK
rW
- sin α · ( ˙ϕz − ϑ˙
z) (2.7)

The derivation can be found in the appendix B.1.

### 2.1.5 Forces

In order to get an idea of the forces taking effect in the system, a Newton/Euler approach

is used to derive analytical equation for the forces shown in figure 2.3. The detailed equations are listed in the appendix B.3.


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
Figure 2.3: Free-body diagrams for the three parts of the model, showing all internal forces

Planar System Modeling and Control | 2.2 Dynamics

### 2.1.6 Parameters

In table 2.1, the parameters describing the system are listed. Numeric values are derived by measuring or from the CAD model. Calculations of the moments of inertia are

presented in section 2.3.2.

Description | Variable | Value
Mass of the ball Mass of the virtual actuating wheel Mass of the body Radius of the ball Radius of the omniwheels Radius of the body (cylinder) Height of the center of gravity Inertia of the ball Inertia of the actuating wheel in the yz-/xz-plane Inertia of the actuating wheel in the xy-plane Inertia of the body Inertia of the body in the xy-plane Gravitational acceleration Gear ratio | mK mW mA rK rW rA l ΘK ΘW ΘW,xy ΘA ΘA,xy g iGear | 2.29 kg 3 kg 9.2 kg 0.125 m 0.06 m 0.1 m 0.339 m 0.0239 kgm² 0.00236 kgm² 0.00945 kgm² 4.76 kgm² 0.092 kgm² 9.81 m/s² 26

Table 2.1: Parameters of the planar system

### 2.2 Dynamics

### 2.2.1 Approach

For the derivation of the equations of motion, the Lagrangian method was selected as the common approach for that kind of problems. The following steps are needed:

- express kinetic (T) and potential (V) energy of all rigid bodies as a function of the

minimal coordinates,

- write non-potential forces as a function of the minimal coordinates,
- solve the Lagrange equation for the second derivative of the minimal coordinates.

The calculations are made for the yz-plane model, which is identical to the xz-plane model, and for the xy-plane model as well.

2.2 Dynamics | Planar System Modeling and Control

### 2.2.2 Energies

The kinetic energy of the ball in the yz-plane contains a translational and a rotational part.

TK,yz =

1
2
- mK · (rK · ϕẋ)

2

| | {z | }
T ranslation

+

1
2
- ΘK · ϕ˙

2
x
| | {z | }
Rotation

(2.8)

The potential energy of the ball is zero, when choosing a coordinate frame in the center of the ball.

VK,yz = 0 | (2.9)

The kinetic energy of the ball in the xy-plane consists of a rotational part only due to the fact that it describes only the rotation around the z-axis. For the same reason, the potential energy for the xy-plane does not need to be considered.

TK,xy =

1
2
- ΘK · ϕ˙

2
z

(2.10)

The kinetic energy of the actuating wheel in the yz-plane is equally composed of a translational and a rotational part, but there is an additional coupling term. The complete derivation of the equations of motion can be found in the appendix B.1.

TW,yz =

1
2

mW

(rKϕẋ)

2
| {z }
T ranslation

+ 2 · (rK + rW ) cos ϑxϑ˙
x(rKϕẋ) + (rK + rW )

2ϑ˙²
x
| | {z | }
| Coupling

+

1
2

ΘW

rK
rW

( ˙ϕx − ϑ˙

x) − ϑ˙
x

2

| | {z | }
| Rotation
(2.11)

The potential energy of the actuating wheel is a simple function of the tilt angle of the body ϑx.

VW,yz = mW · g · (rK + rW ) cos ϑx | (2.12)

For the xy-plane, the kinetic energy of the motor and wheel is similar to that of the ball.

TW,xy =

1
2
- ΘW,xy · ψ˙²
z

(2.13)

Planar System Modeling and Control | 2.2 Dynamics

The energies of the body are again very similar to the ones of the actuating wheel.

TA,yz =

1
2

mA

(rKϕẋ)

2 + 2 · l cos ϑxϑ˙
x(rKϕẋ) + l

2ϑ˙²
x
+

1
2

ΘAϑ˙²
x

(2.14)

VA,yz = mA · g · l · cos ϑx | (2.15)

TA,xy =

1
2
- ΘA,xy · ϑ˙² z | (2.16)

### 2.2.3 Non-Potential Forces

Non-potential forces fNP represent the external forces acting on a system. In this case, the motor torque Tx i.e. the system input is a non-potential force. The motor torque takes a direct effect on the coordinate ψx. Using equation (2.5), the effect of the motor

torque on the minimal coordinates can be expressed:

~fNP,yz1 =

" rK
rW
- Tx
−
1 + rK
rW
Tx
(2.17)

The counter torque acting on the coordinate ϑx of the body is expressed as:

~fNP,yz2 =

"
0
Tx
(2.18)

The total non-potential force is then the sum of ~fNP,yz1 and ~fNP,yz2. A similar procedure

is applied in the xy-plane. In this model, an additional friction force Tf is acting on ϕz as the rotation of the ball:

~fNP,xy =

"
−Tf +

rK
rW
- sin α · Tz
−

rK
rW
- sin α · Tz + Tz
(2.19)

### 2.2.4 Equations of Motion

Now, the equations of motion are derived by solving the Lagrange equation for ¨~q.

d
dt
∂T
∂

˙~q T
−
∂T

∂~q T
+
∂V

∂~q T
− ~fNP = 0 | (2.20)

T and V denote the total kinetic and potential energy respectively.

T = TK + TW + TA

V = VK + VW + VA

2.3 Conversions to the Real System | Planar System Modeling and Control

Finally, the equations of motion for the planar inverted pendulum in the yz-plane can be written in matrix form as follows.

Mx(~q, ˙~q)

¨~q + Cx(~q, ˙~q) + Gx(~q) = fNP | (2.21)

The matrices containing masses and inertias Mx, Coriolis forces Cx and gravitational forces Gx are:

Mx =

mtotr

2
K + ΘK +
rK
rW

2
ΘW −

rK
r

2
W

rtotΘW + γrK cos ϑx

−

rK
r

2
W

rtotΘW + γrK cos ϑx

r

2
tot
r

2
W
| ΘW + ΘA + mAl

2 + mW r

2
tot
- (2.22)

Cx =

"
−rKγ sin ϑxϑ˙2
x
0
(2.23)

Gx =

"
0
−g sin ϑxγ
(2.24)

The following substitutions were used in the equations above.

mtot = mK + mA + mW

rtot = rK + rW

γ = l · mA + (rK + rW )mW

The Lagrange equation of the planar model in the xy-plane solved for ϕ¨z and ϑ¨ z yield
the following equations of motion.

ϕ¨z = −

(r

2
W ΘA,xy + r

2

KΘW,xy sin² α) · Tf + rKrW ΘA,xy sin α · Tz

r

2
W ΘA,xyΘK + r

2

K(ΘA,xy + ΘK)ΘW,xy sin² α

(2.25)

ϑ¨
z = −

rK sin α(rKΘW,xy sin α · Tf + rW ΘK · Tz) r

2
W ΘA,xyΘK + r

2

K(ΘA,xy + ΘK)ΘW,xy sin² α

(2.26)

To compute the friction force, it is assumed that the ball always sticks on the ground, thus the condition for stiction ϕ¨ = 0 has to be fulfilled. With equation (2.25), Tf can be

written as follows:

Tf =

rKrW ΘA,xy sin α · Tz
r

2
W ΘA,xy + r

2

KΘW,xy sin² α

(2.27)

### 2.3 Conversions to the Real System

### 2.3.1 Torque Conversion

The planar model uses a virtual wheel to actuate the system. The real system has an actuating structure which differs strongly from the one assumed in the planar model.

Planar System Modeling and Control | 2.3 Conversions to the Real System

Since a controller for the planar model is going to be implemented on the real system,

conversions have to be calculated. In order to be able to control the real system, the
torques on the virtual motors have to be converted into the torques for the real motors.

Definitions

One element of the real system (omniwheel driven by a motor) is shown on the left side

in figure 2.4. It actuates the ball by scrolling on a circle on the ball, characterized by the motor arrangement angle α.
The right side of figure 2.4 shows a top view on the real actuating system where the torque of each omniwheel generates a tangential force on the surface of the ball.

## cosα

sinα

Ti

## rK sinα

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
Figure 2.4: On the left side the arrangement of one real omniwheel is shown. The sketch on the right side shows the torques and tangential forces generated by the real actuating system, the dashed arrows mark the virtual torques.

FW,1, FW,2, FW,3 in figure 2.4 denote the tangential forces on the ball generated by torques of the motors in the real configuration, consequently these are functions of T1,2,3. The levers for this configuration are denoted as rKW,1, rKW,3, rKW,3. For the virtual configuration, the notation FW,x, FW,y, FW,z is used for the tangential forces (as functions of Tx,y,z) and rKW,x, rKW,y, rKW,z for the levers. All those are geometrical

relationships one can read out of figure 2.4. In the appendix C.1 the relationships are written out in full.

2.3 Conversions to the Real System | Planar System Modeling and Control

Torque on the ball

Once the relationships are given, the torque on the ball from the real and the virtual driving mechanism can be calculated. The torque is equal to the product of force and lever. Hence the torques for the real and the virtual configuration are calculated as follows.

TKW,i = rKW,i × FW,i | for i = 1, 2, 3 | (2.28)
TKW,j = rKW,j × FW,j | for j = x, y, z | (2.29)

Solution

Of course, the overall torque needs to be conserved:

TKW,1 + TKW,2 + TKW,3 = TKW,x + TKW,y + TKW,z | (2.30)

Solving the relations for the real torques yields:

T1 =

1
3

·

Tz +

2
cos α
- (Tx · cos β − Ty · sin β)
(2.31)

T2 =

1
3

·

Tz +

1
cos α

·

sin β · (−

√
3Tx + Ty) − cos β · (Tx +

√
3Ty)
(2.32)

T3 =

1
3

·

Tz +

1
cos α

·

sin β · (

√
3Tx + Ty) + cos β · (−Tx +

√
3Ty)
(2.33)

Since the system of equation is linear in Tx,y,z, it is straightforward to solve for them as well (see appendix appendix C).

### 2.3.2 Inertia Calculations

The aim of this section is to find a suitable approximation for the moments of inertia of the modeled drive mechanism, which is not the same as in reality. The following approach is made by comparing the energies stored in the real omniwheels and the virtual actuating wheel respectively when driving at a constant velocity.

Approximations for sphere and body

The inertia of the ball is approximated by a hollow sphere, which is a good approximation:

ΘK =

2
3
- mK · r

2
K

The moment of inertia of the body was initially approximated by that of a cylinder. Later, it was directly calculated in the CAD model.

Planar System Modeling and Control | 2.4 Development of a Planar Model Based Controller

Conversion for motors and omniwheels

The real rotor inertia of a motor is given by

ΘM = 3.33 · 10⁻⁶
kgm²

and the real inertia of an omniwheel is calculated as:

ΘOW =

1
2
- mOW · r

2

W = 900 · 10⁻⁶
kgm²

Since the reduction of the gear box is i = 26, the rotor of the motor turns 26 times faster. Therefore, a factor i

2
is added to calculate the energy (E =

1/2· Θ · v

2
). So both,

omniwheel and motor inertias are taken into account. The inertia of the gear rotor is 9.1 · 10⁻⁶ kgm²
and therefore negligible.
In order to obtain an approximation of the inertia of the virtual actuating wheel ΘOW,x, the rotation speed of each real omniwheel is calculated, while turning the virtual omniwheel at a specific speed. The rotational energy of the virtual wheel is then equated to the sum of the energies of the real wheels. This equation can be solved for the virtual inertia. The following results were obtained:

ΘW,x = ΘW,y =

3
2
- cos²
(α)(ΘOW + i

2
- ΘM) | (2.34)

ΘW,z = 3 · (ΘOW + i

2
- ΘM) | (2.35)

Comparing the numerical values for the energies of the ball, the actuating wheel and the body (assuming speeds of v = 3 m/s and ϑ˙
x = 1 rad/s) shows that all three values have the same order of magnitude (equations 2.36–2.38). Hence, it is appropriate to take all

these energies into account for the modeling.

EK = 6.88 J | (2.36)
EA = 1.48 J | (2.37)
EW = 2.95 J | (2.38)

### 2.4 Development of a Planar Model Based Controller

### 2.4.1 System Analysis

Based on the model introduced above, a linear controller is designed. Therefore, the equations have to be linearized. In order to obtain the linear equations, the equations of motion are written in state space form (2.39).

˙~x =

"
~q

˙~q#˙
=

"
˙~q

M⁻¹
x

(fNP − (Cx + Gx))#
(2.39)

2.4 Development of a Planar Model Based Controller | Planar System Modeling and Control

Since the expected operating point values and input signals have the same order of magnitude, no normalization is used.²
With the state vector ~x = [ϕx, ϑx, ϕẋ, ϑ˙
x], the input u = Tx and the system output

~y = ~x, meaning that the output is equal to the states, because all states are measured

with the sensors, the linearized state space description is

˙~x =A · ~x + B · ~u , | ~y = C · ~x + D · ~u . | (2.40)

Next, the matrices can be derived using a Taylor expansion of the equation of motion. Substituting the variables with numerical values, one gets the following matrices for the yz-plane/xz-plane model:

A =

0 | 0 | 1 0
0 | 0 | 0 1
0 −31.4603 0 0
0 | 16.3333 | 0 0

B =

0
0
13.4993
−2.8567

C =

1 0 0 0
0 1 0 0
0 0 1 0
0 0 0 1

D =

0
0
0
0

The controllability matrix as well as the observability matrix have full rank, which means that the system is fully controllable and fully observable and thus stabilizable. One pole of the system with positive real part show its instability. Similar to an inverted pendulum, a ballbot has a non-minimum phase behavior.[1]

Carrying out the linearization for the xy-plane model in an equivalent way yields:

A =

0 0 1 0
0 0 0 1
0 0 0 0
0 0 0 0

B =

0
0
0
−17.2267

C =

1 0 0 0
0 1 0 0
0 0 1 0
0 0 0 1

D =

0
0
0
0

### 2.4.2 Controller Design

For the two planar inverted pendulums a linear quadratic state feedback controller (LQR)

is designed. In the LQR problem a solution minimizing the cost criterion

J(u) = Z ∞

0

x

T
(t) · Q · x(t) + u

T
(t) · R · u(t)
dt | (2.41)

is sought.[2] In order to apply LQR, full state feedback is used. In many systems it is

hard to measure all states and therefore a model based observer has to be used. If all
states are available, the solution is u(t) = −K · x(t), where K = R⁻¹ | · B · Φ and Φ is

the only positive definite solution of the Riccati equation:

Φ · B · R

−1
- B

T
- Φ − Φ · A − A

T
- Φ − Q = 0 | (2.42)

2Normalization is used for preventing numerical problems.

Planar System Modeling and Control | 2.4 Development of a Planar Model Based Controller

Since all states are estimated by the sensors in the system discussed, the application of an
LQR controller is straightforward. The weighting matrices Q and R are experimentally
tuned (view section 2.4.3). For given Q and R matrices, the controller gains K can be

derived using the MATLAB lqr command. Since the LQR controller is designed for a set point equal to zero, an additional factor to the set point is needed, in order to achieve a correct tracking behavior. This gain is calculated as proposed in [3]:

N = −

C(A − BK)

−1B

−1
| (2.43)
N | B

A

K

∫ | C
+ | +
– | +
r | x | y

P

Figure 2.5: Block schema of the LQR controller with the linear model P (shaded in grey)

Three different controllers are implemented on the system. First, a position controller which uses all states to stabilize the system and accepts position set points. Furthermore, a velocity controller that does not stabilize the position, thus only uses the states x = [ϑx, ϕẋ, ϑ˙
x], is implemented. Finally, an angle controller which uses solely the states x = [ϑx, ϑ˙
x] and no information about position and speed.

For the relatively simple xy-plane model, a PD controller is experimentally developed. With the parameters kp = −0.5 and kd = −0.3, the rotation angle ϑz can be stabilized.

Because of developing a controller for the full three dimensional system, these parameters were not tuned any further.

### 2.4.3 Tuning on the Real System

The initial guess for the weighting matrices Q and R, which worked well for the simulation, was found to be much too aggressive to be applied on the real system. The problem is, that the noise on the gyroscope values (corresponding to the state ϑ˙) is amplified by

the controller and thus causes the system to start trembling also linked with backlash of the gear box. Therefore, in order to lower the controller gains, the parameter R was iteratively increased. In addition, the damping coefficients, i.e. the factors in the matrix Q, which weights the velocities, were raised too. Finally, the following matrices are found

2.4 Development of a Planar Model Based Controller | Planar System Modeling and Control

to generate controller gains which stabilize the ballbot without causing trembling:

Q =

20 | 0 | 0 | 0
0 | 100 | 0 | 0
0 | 0 | 10 | 0
0 | 0 | 0 | 50

R = 200

The controller gains calculated with these weighting matrices are:

K =

h

−0.3162 −22.8608 −0.5359 −6.5726i

In order to improve the performance of the controller, a finite impulse response (FIR) low-pass filter of fourth order with a cutoff frequency of approximately 15 Hz (view section 3.4.2) is applied on the controller output. Therefore the gains can be increased,

while the system remains stable.
Finally, the controller gains are slightly modified by hand to improve the performance. The gains used in the end are the following:

K =

h

−0.8944 −60 −1.5 −10i

Simulation and Verification of the Planar Model

## 3 Simulation and Verification of the Planar Model

### 3.1 Implementation in Simulink

The nonlinear equations of the planar model are implemented in Simulink (fig. 3.1) for

model verification. First, simulations without controller showed that the system behaves as expected. The simulation is also used to develop and test the controller and any further software that is going to be implemented on the real system. Therefore, the

VR Sink; Bot.translation; Pendl_z.rotation; Pendl_x.rotation; Pendl_y.rotation; Wheel1.rotation; Wheel2.rotation; Wheel3.rotation; Sphere.rotation; Umrechnungen; states_z; states_x; states_y; position; z_rotation; x_rotation; y_rotation; ow1_rotation; ow2_rotation; ow3_rotation; ball_rotation; time; Sollwert Generator; angle_x; angle_y; angle_z; Sollwert Filter; Regler; Modell Ballbot; T_z states_y; theta_x; theta_dot_x; phi_ddot_x; theta_ddot_x; states_z states_x; Kraefte; theta; theta_dot; phi_ddot; theta_ddot; Clock

simulation should fit the reality as precisely as possible. In section 3.3 the approach to improve the simulation in that way is explained.

Figure 3.1: Simulink block scheme of the complete simulation environment

For handling the simulation a simple to use graphical user interface (GUI) is programmed in MATLAB (figure 3.2), where the control method and the input can be chosen. When starting the simulation, the real time visualization (section 3.2) is shown. After the

simulation is stopped, the plots are generated.

### 3.2 Visualization

To visualize the data generated in the simulation, the 3D Animation Toolbox of MATLAB is used, which is a relatively simple way to achieve a three-dimensional visualization of the model in real time. Figure 3.3 shows a screenshot of the visualization.


3.2 Visualization | Simulation and Verification of the Planar Model

Figure 3.2: Screenshot of the GUI for the simulation environment

Figure 3.3: Screenshot of the virtual reality environment in Simulink

Simulation and Verification of the Planar Model | 3.3 Error Model

### 3.3 Error Model

To get an idea of the effect of noise and delay occurring in the real system, simple assumptions are made and simulated in Simulink.

### 3.3.1 Noise

The only noise that is assumed to be relevant is the sensor noise from the angle estimation and from the gyroscopes of the IMU. The discretization error of the motor encoder is neglected. The dynamic IMU noise is measured by rotating the IMU constantly around each axis separately. It is assumed that the rotation contains no high frequency oscillating, therefore, by subtracting the rotation speed from the measured data, the magnitude of the dynamic noise can be estimated. As shown in figure 3.5, the magnitude measured in this test is approximately ±0.05 rad/s at a sample time of 157.8 Hz. This data is then directly added to the angle rate (signal n in figure 3.4).

Figure 3.4: LQR feedback control schema with sensor noise n

### 3.3.2 Delay

In addition to the sensor noise, a delay of 0.01 s is added to the plant, representing the delay occurring in the real system by signal processing (a sample rate of 160 Hz means a maximum delay of 0.007 s).

### 3.4 Filtering

As already discussed in section 2.4.3, noise and other non-ideal effects are the main reason why the controller cannot be tuned in the desired way. Particularly the noise is limiting the magnitude of the controller gains and therefore the performance of the controller. In order to counteract these undesired effects, different solutions are tried.

3.4 Filtering | Simulation and Verification of the Planar Model

Figure 3.5: Measured data from the IMU gyroscopes, showing the noise.

### 3.4.1 Offset

Because of the friction, the motors do not start turning unless they get more than a specified amount of torque as input. The current needed to start the motors turning is experimentally determined and amounts to approximately 80 mA, what corresponds to a input torque of 42 mNm. An offset with that threshold was tested on the ballbot without improvement and is therefore not used.

### 3.4.2 Low Pass Filter

The noticeable amount of noise on the gyroscope values (fig. 3.5) causes the output of

the controller to be very noisy too, which is shown by a trembling of the system. By applying a low pass filter on the controller output, this effect is eliminated. The low pass is derived using the Filter Design Toolbox fdatool of MATLAB. It is a fourth order finite impulse response (FIR) filter with a cutoff frequency of approximately 15 Hz.

### 3.4.3 Kalman Filter

By applying a Kalman filter on the sensor values and estimating the gyroscope values using the model, it is also possible to eliminate the trembling. As can be see in figure 3.7, it has the same effect as the low pass filter, whereas it does not cause as much delay as the low pass filter. The development of a Kalman filter is part of the bachelor thesis [4].

Simulation and Verification of the Planar Model | 3.5 Verification of the Planar Model

Magnitude (dB); Frequency (Hz)

Figure 3.6: Magnitude of the transfer function of the fourth order lowpass filter

### torque motor one

time [s]; torque [Nm]; kalman filtered; without filter with lowpass filter

Figure 3.7: The raw signal (blue), the low pass filter signal (green) and the Kalman filter signal (red) of the system input

### 3.5 Verification of the Planar Model

A velocity step applied to the real system and to the planar model is shown in figure
3.8. The velocity step in this case is generated using a positive set point for ϕẋ, which is equal to an actual translation in the direction of the y-axis. So actually it is a planar problem. The agreement of the step responses is generally quite good. The small deviations between the measured data and the simulated data are mainly due to noise and simplifications in the model. To perform this step with the prototype, a controller

3.6 Drawbacks on the Planar Model | Simulation and Verification of the Planar Model

based on the planar model was implemented. The same controller is used in the model. Therefore, it is not a feed forward verification as usually done. However, that would not be possible on an unstable system. Obviously, this controller is able to stabilize the system and to achieve an acceptable performance. Therefore, the model is a reasonable representation of the system. Further plots can be found in the appendix F.1.

0 | 2 | 4 | 6 | 8 | 10 | 12 | 14 | 16 | 18

−1

−0.5

0

0.5

1

1.5

2

2.5

3

### time [s]

φ

## x dot [rad/s]

### velocity step

Figure 3.8: System and model response on a velocity step from 0 rad/s to 1.5 rad/s for 4 s

### 3.6 Drawbacks on the Planar Model

By splitting the system into three separate planar models, the coupling effects between the models are neglected. It can be shown that when driving into the y-direction (yz-plane) and then turning about the z-axis (xy-plane), there is no effect to the xz-plane model (fig. 3.9). It is intuitively clear that such a behavior does not represent reality.

Another drawback of the planar system modeling is that a lot of conversions have to be done (see chapter 2.3) to get the real system working. And for example the moments of

inertia calculations are simple approximations.

Simulation and Verification of the Planar Model; 3.6 Drawbacks on the Planar Model; time [s]; x dot [rad/s]; velocity step; model setpoint; y dot [rad/s]; z [rad]

Figure 3.9: The response of the model to a velocity step in x direction (center) and a ramp on the

rotation around the z-axis (bottom)

3D System Modeling and Control

## 4 3D System Modeling and Control

The representation of the real system of a ballbot as a planar model implies multiple drawbacks as described in section 3.6. The interconnecting effects between the planar models could be added separately to the dynamic equations and the results be verified subsequently. However, the approach described in this chapter takes the real, full three-dimensional geometry and parameters into account. With this model, all coupling effects are considered and no artificial conversions are required.

### 4.1 Model

### 4.1.1 Model Description

Geometry

## Body

## Motor with gear head

## Omniwheel

## Ball

Figure 4.1: Geometrical representation of the 3d model

The proposed 3d model as shown in figure 4.1 consists of five solid bodies:

- 1 ball,
- 3 omniwheels,
- 1 body with 3 motors with gear head.

The ball can rotate about any axis parallel to the ground but not about the vertical axis. It is always in contact with the ground in one arbitrary point. Three omniwheels link the upper system to the ball in three points at any time. Each of these wheels is fixed to the

4.1 Model | 3D System Modeling and Control
| body over a motor with a gear head. The omniwheels can solely rotate about the motor
| axis in reference to the body coordinate system. The linkage between the wheels and
| the ball is holonomic and the wheel can only apply forces to the ball in the tangential
direction of its rotation in the body reference system.
| This system can be described with the following five degrees of freedom (DoF):
- 2 DoF for the position of the ball,
- 3 DoF for the rotation of the body.
| All other geometrical coordinates, e.g., the rotation of the omniwheels, can be calculated
| directly from the given five states. A detailed description of these binding equations is
given in section 4.1.4.

Input and Output

| The inputs to the system are the three torques T1, T2, T3 which are generated by the
motors and transformed by the gear heads.
| The sensors of the system are chosen in a way that all states can be measured directly.
| Therefore, each output represents a state separately. Details on the output variables are
given in 4.3.2.
| This system has several inputs and outputs and can be characterized as a MIMO¹ system.

### 4.1.2 Assumptions

| In addition to the geometrical simplification of the system, the same assumptions as in
the planar model are made (see 2.1.2).
| Since the rotation of the ball about the vertical axis is not modeled, high rotational
| stiction at the contact point between ball and ground has to be assumed or guaranteed
| by limiting the torque around the z-axis by appropriate motor torque setting.

### 4.1.3 Coordinates

| The inertial reference frame is denoted as I (see fig. 4.2). By turning about the inertial

z-axis e

I
| z with ϑz, the reference system denoted as L is described. The reference systems
A⁰
| is derived from the rotation about the y-axis in the L-system e L y with ϑy. Finally, the
| body fixed reference system is denoted as A and is derived from the rotation about the
x-axis in the A⁰
-system e

A⁰
x with ϑx.
| The representation of the coordinate systems in the Euler form is chosen because the
| following calculations are well know in this form. Furthermore, the system is supposed to operate in the range of tilt angles of maximum ±20◦ , in which singularities do not

1Multiple Input, Multiple Output

3D System Modeling and Control | 4.1 Model

have to be considered. The sequence of the transformations as Tait-Bryan angles²
are
matched with the convention of the sensor output, making conversions unnecessary.

L

ΩK

I | L | À | A

O

ϑ

z | ϑy | ϑx

Figure 4.2: Coordinate systems (left) and angular velocities (right)

The angular velocity vectors of the bodies are denoted as follows:

- Ω~ K: Angular velocity of the ball
Parametrization of Ω~ K in the reference system L:

LΩ~ K =

ϕẋ
ϕ˙ y
0

- (4.1)

ϕẋ, ϕ˙ y are not the variations of any orientation angles of the ball. They are the parametrization of the angular velocity of the ball LΩ~ K and are named to match

the notation of the planar system.

- ωW i: Angular speed of an omniwheel i relative to the reference system A in direction of the motor axis
Parametrization of ωW i:

AωW1 = ψ˙

1 | AωW2 = ψ˙
2 | AωW3 = ψ˙
3 | (4.2)

2
specific kind of Euler angles often used in aerospace applications

4.1 Model | 3D System Modeling and Control
- Ω~ A: Angular velocity of the body
| In order to express the angular velocity of the body with the variables ϑx, ϑy and ϑz, the time variation of the Tait-Bryan angles ˙ ϑ~ needs to be converted with the
| Jacobian matrix J (see [6] for further explanations).
| Parametrization of Ω~ A in the reference system A:

AΩ~ A = J ·

˙
ϑ~ =

ϑ˙

x − sin ϑy · ϑ˙
z
cos ϑx · ϑ˙

y + cos ϑy · sin ϑx · ϑ˙
z
− sin ϑx · ϑ˙

y + cos ϑx · cos ϑy · ϑ˙
z

- (4.3)

### 4.1.4 Binding Equations

The system described has five degrees of freedom, as discussed in 4.1.1. Geometrical dependencies have to be formulated with the aim to express all other geometrical variables as terms of the primary representation of the system.
The primary representation is chosen as ϑx, ϑy, ϑz, ϕx, ϕy. This choice renders in a solution more compact than other alternatives (see 4.3.1). It is important to distinguish

that while ϑx, ϑy and ϑz are spatial orientation angles, ϕx and ϕy are simply the integral of the parametrization of the angular velocity of the ball LΩ~ K. ϕx and ϕy do not

represent the orientation of the ball but the rolled angles in the respective direction.

Absolute rotation of the omniwheels

As a first step, the absolute rotation of the omniwheels are calculated. The vectors from the intersection of the motor directions M to the center point of the omniwheels W1, W2 and W3 in the body fixed reference system A are denoted as A

−−−→MW1, A

−−−→MW2 and

A

−−−→MW3 (fig. 4.3).

Figure 4.3: Geometrical points for the binding equations

3D System Modeling and Control | 4.1 Model

The absolute angular speed of the omniwheels about the motor axis in the body reference
frame A can now be written as

AΩW i = AωW i +

A

−−−→MWi

||A

−−−→MWi
- AΩ~ A | for i = 1, 2, 3. | (4.4)

Dependency on the rotation of the omniwheels

The vectors from the center of the ball P to the contact point with the omniwheels K1, K2 and K3 in the reference system A are denoted as A

−−→PK1, A

−−→PK2 and A

−−→PK3, the

directions of the tangential velocity of the rotation of the omniwheels as unit vectors

A

~d1, A

~d2 and A

~d3.

The angular velocity of the ball relative to the body in the reference system A can be

calculated as

A~ωK = RAL · LΩ~ K − AΩ~ A | (4.5)

where RAL is the transformation matrix from the reference system L to A.

Based on the no slip assumption, it follows: The speed on the surface of the ball in omniwheel direction has to be the same speed as the tangential speed of the omniwheel itself. This can be formulated as a scalar equation for each omniwheel:

(A~ωK × A

−−→PKi) · A
~di = AωW i · rW | for i = 1, 2, 3, | (4.6)

where rW denotes the radius of the omniwheel. Solving these equations for AωW1, AωW2 and AωW3 results in explicit statements depending on ϑx, ϑy, ϑz, ϑ˙

x, ϑ˙

y, ϑ˙
| | z, ϕẋ and
ϕ˙ y.

Finally, AΩW1, AΩW2 and AΩW3 can easily be calculated. The solution for AΩW2 is given as an example:

AΩW2 =

1
2

√
2 · rW
- (rK · (cos ϑy + (2 cos ϑx −

√
3 sin ϑx) · sin ϑy) · ϕẋ

− rK · (

√
3 cos ϑx + 2 sin ϑx) · ϕ˙ y + (rK + rW ) · (−ϑ˙

x + (√
3 cos ϑx+

2 sin ϑx) · ϑ˙
y + (cos ϑy · (−2 cos ϑx +

√
3 sin ϑx) + sin ϑy) · ϑ˙
z))

All detailed calculations and solutions are shown in E.

Based on exactly the same ideas but calculated and solved in a different order, a solution for the odometry calculation is found. The odometry calculations and solutions are shown in detail in D.

4.1 Model | 3D System Modeling and Control

Translation of the ball

| It is important to know the translational speed of the ballbot for later calculations. Also,
| integrating the translational speed generates information about the exact location of the
ballbot relative to the inertial reference system I.
| Knowing the vector from the ground B to the center of the ball P, I −−→BP, the speed

vector I

| ˙~rP of the center of the ball P can be calculated as

I

˙~rP = IΩK × I

−−→BP . | (4.7)

### 4.1.5 Parameters

In the following section all parameters additional to table 2.1 are described.

Description | Variable | Value
Inertia of the ball Inertia of the body Inertia of the body Inertia of the body Inertia of one motor and wheel Angle of the omniwheel contact point Angles of the omniwheel directions | ΘK ΘA,x ΘA,y ΘA,z ΘW α β1, β2, β3 | 0.0239 kgm² 2.026 kgm² 2.025 kgm² 0.092 kgm² 0.00315 kgm² 45◦ 0 ◦ , 120◦ , 240◦

Table 4.1: Additional parameters of the 3d system

The moments of inertia for the ball and the body, ΘK and ΘA respectively, are tensors and are given at the center of the ball. They are chosen in a reference system (see 4.1.3),

where the principal moments of inertia become zero.

IΘK = LΘK =

ΘK | 0 | 0
0 | ΘK | 0
0 | 0 | ΘK

- (4.8)

AΘA =

AΘA,x | 0 | 0
0 | AΘA,y | 0
0 | 0 | AΘA,z

- (4.9)

The moment of inertia for a motor with an attached omniwheel ΘW , is a scalar and is given solely for the rotation about the motor axis in the body fixed coordinate system. In order to consider the rotation of the motors and omniwheels about all axes in the inertial reference frame, their moment of inertia is simply added to the moment of inertia for the body. This results in a simplified description for the system energies (see 4.2.1).

However, gyroscopic effects, especially at high angular speed, are not taken into account with this simplification.

3D System Modeling and Control | 4.1 Model

Of course, as described in section 2.3.2, it is necessary to take the gear ratio between
motor and omniwheel into consideration. Equation (4.10) describes the relation for the

moment of inertia of an omniwheel ΘOW and the corresponding motor ΘM.

ΘW = ΘOW + i

2
gear · ΘM | (4.10)

l

g

## mW, ΘW

## mK, ΘK

Figure 4.4: Geometrical parameters of the 3d systems


3

2

Figure 4.5: Angles of the motor configuration

4.2 Dynamics | 3D System Modeling and Control

### 4.2 Dynamics

This section describes the derivation of the dynamic equations which are needed for analysis, simulation and the design of a suitable controller.
As with the planar system modeling, the Lagrangian method is used to derive the equations of motion (see 2.2.1). As minimal coordinates ~q the following set of variables

is used:

~q =

h
ϑx | ϑy | ϑz | ϕx | ϕy

iT
(4.11)

### 4.2.1 Energies

For each body, translational, rotational and potential energies have to be considered. The plane with zero potential energy is chosen to concur the center of the ball.

Ball

The kinetic energy of the ball consists of a translational and a rotational part.

TK =

1
2
- mK · I
| | ˙~rT
P
| | | · I | ˙~rP
| | | {z | | }
T ranslation
| | | | +

1
2
- LΩ~ T

K · LΘK · LΩ~ K

| | {z | }
Rotation

(4.12)

The ball is only moving in the horizontal directions (see 2.1.2), meaning that its potential

energy VK is zero at any time.

Body

As explained in section 4.1.5, in mA and ΘA the motors and omniwheels are also considered.
The point of reference is chosen in P, which is not the center of mass, in comparison to the calculation of the ball. As a result, a coupling term has to be included.

TA =

1
2
- mA · I

˙~rT
P
- I

˙~rP

| | {z | }
T ranslation

+ mA · (RAI · I

˙~rP ) · (AΩ~ A × A~rP SA)
| | {z | }
Coupling

+

1
2
- AΩ~ T

A · AΘA · AΩ~ A

| | {z | }
Rotation
(4.13)

A~rP SA denotes the vector from the center of the ball P to the center of gravity of the body SA in the reference system A.
The potential energy of the body including motors and omniwheels is calculated as
VA = −mA · G~ · RIA · A~rP SA | with G~ =

0
0
−g

- (4.14)

3D System Modeling and Control | | 4.2 Dynamics

Omniwheels

The additional rotation of the omniwheels and the motors around the respective motor axis is modeled here. As a result of the simplification made in section 4.1.5, only the rotational energies have to be considered.

TW i =

1
2
- AΘW i · AΩ

2
W i | for i = 1, 2, 3 | (4.15)

### 4.2.2 Non-Potential Forces

The non-potential forces fNP are of course the motor torques T1, T2 and T3, which are used to stabilize the system. They act directly on AωW1, AωW2 and AωW3 respectively. Since the parameters ψ˙

1, ψ˙

2 and ψ˙
3 are not components of the minimal coordinates ~q, a

polynomial separation has to be done, such that

AωW i = JT i ·

˙~q | for i = 1, 2, 3 | (4.16)

is fulfilled.
Also, it is important to consider the counter torques acting on the body T~C,1, T~C,2 and T~C,3. They act on the opposite direction of T1, T2 and T3 respectively and are formulated

as shown in (4.17).

T~C,i =

A

−−−→MWi

||A

−−−→MWi
- (−Ti) | for i = 1, 2, 3 | (4.17)

The associated Jacobian matrix is derived in (4.3) and is here denoted as JT C.

Hence, the non-potential forces fNP can be written as

fNP = J

T
T1
- T1 + J

T
T2
- T2 + J

T
T3
- T3 + J

T

T C · (T~C,1 + T~C,2 + T~C,3). | (4.18)

### 4.2.3 Equations of Motion

The equations of motion are now derived by solving the Lagrange equation, analogously to the planar procedure.

d
dt
∂T
∂

˙~q T
−
∂T

∂~q T
+
∂V

∂~q T
− ~fNP = 0 | (4.19)

with

T = TK + TA + TW1 + TW2 + TW3

V = VA

4.3 System Analysis | | 3D System Modeling and Control

At this point it is important to note that these calculations could not be done directly in a software package like Mathematica. Instead, the calculations had to be separated into multiple, smaller computations and simplified after each step.

### 4.3 System Analysis

### 4.3.1 Nonlinear System

The equations of motion for the system described in section 4.2.3 are a set of vast, nonlinear, ordinary differential equations. They consist of thousands of terms and cannot be overviewed by any means.
The first 3d models also considered the rotation of the ball about the vertical axis and used different minimal coordinates. As a consequence, the results rendered in a file size over 40 MB when saved as a simple text file. With the model introduced in chapter 4.1.1, the file size is brought down to 0.5 MB and can be simulated in real time. Because of the size of this complex system, its analysis is limited to a linearized version of the system.

### 4.3.2 Linearized System

For the state space representation (4.20), the state vector ~x, the input vector ~u and the output vector ~y are chosen as shown in (4.21)–(4.23). As in section 2.4.2, the process of

normalization is left out, because all states, inputs and outputs have the same order of magnitude.

˙~x =A · ~x + B · ~u | ~y = C · ~x + D · ~u | (4.20)

~x =

h
ϑx | ϑ˙
x | ϑy | ϑ˙
y | ϑz | ϑ˙
z | ϕx | ϕẋ | ϕy | ϕ˙ y

iT
(4.21)

~u =

u1
u2
u3

- =

T1
T2
T3

- (4.22)
~y =~x | (4.23)

Linearization at zero

As a first step, it makes sense to linearize all states at zero, because the ballbot is controlled to keep the body upright and the position constant. Furthermore, a ballbot can tilt and drive in any direction, so linearization around zero is a reasonable trade-off. Additionally, it is the unstable equilibrium of a ballbot.

3D System Modeling and Control | 4.3 System Analysis


Figure 4.6: Matrices A0 and B0 for the linearization at zero for all states. The subsystem for the planar model in the yz-plane is marked blue, for the xz-plane red and for the xy-plane black.

The matrix C0 is a 10 × 10 identity matrix and D0 is a 10 × 3 zero matrix. The stability and non-minimum phase behavior is similar to the planar model (see 2.4.1).

Figure 4.6 shows that the 3d system linearized at zero can be split into three independent planar systems. The red and blue marked entries of A0 and B0 are the two identical systems for the yz- and xz-plane (see 2.1.2) and the black marked entries represent the

system for the xy-plane. The slight numerical difference in A0 for the yz- and xz-systems originates in the difference of their respective moment of inertia.
Also, it can be clearly seen by observing the matrix B0 that the motors exert different influences on each system. For example, u1 (from motor 1) has the main effect on the yz-system, while u2 and u3 (from motor 2 and 3) have a smaller and opposite

input. Likewise, u1 has no influence on the xz-system, because its omniwheel stands perpendicular to the ball turning direction of this configuration.

Linearization at an arbitrary point

To show the influence of the choice of the linearization point, an arbitrary operation point (4.24) is chosen as linearization point.

4.3 System Analysis | 3D System Modeling and Control

The parameters ϑz, ϕx and ϕy reflect the orientation and position of the ballbot and are therefore irrelevant for its dynamics. Hence, their linearization point has no influence on the state space matrices.
For all other states, the following linearization point is chosen:

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
ϕ˙ y

=

0.32 rad
−0.5 rad/s

0.1 rad
0.35 rad/s
−0.2 rad/s
6.3 rad/s
2.3 rad/s

u1
u2
u3

- =

1.1 Nm
−3.3 Nm
−2.7 Nm

- (4.24)

With n denoting an arbitrary operation point, the state space matrices Cn and Dn are the same as before, An and Bn are shown in 4.25 and 4.26 respectively. By comparing the matrices to figure 4.6, it is obvious that An and Bn describe different systems and exhibit strong coupling terms.

An =

0 | 1 | 0 | 0 | 0 | 0 | 0 | 0 | 0 | 0
12.85 | −0.5234 | 64.1 | 1.164 | 0 | 2.361 | 0 | 0.09295 | 0 | 0.07759
0 | 0 | 0 | 1 | 0 | 0 | 0 | 0 | 0 | 0
−62.57 | 3.008 | 32.44 | −5.953 0 −3.789 0 −0.1806 0 −0.4806
0 | 0 | 0 | 0 | 0 | 1 | 0 | 0 | 0 | 0
−38.94 | −8.147 | 4.429 | 21.06 | 0 | 6.915 | 0 | 1.066 | 0 | 1.703
0 | 0 | 0 | 0 | 0 | 0 | 0 | 1 | 0 | 0
−13.2 | −1.236 | −28.15 | 1.551 | 0 −2.268 0 | 0.03377 | 0 | 0.1916
0 | 0 | 0 | 0 | 0 | 0 | 0 | 0 | 0 | 1
45.18 | 0.3581 | −42.06 | −3.098 0 | 3.54 | 0 −0.3492 0 | −0.206

| | | | | | | | | (4.25)

Bn =

0 | 0 | 0
2.327 −2.863 −3.038
0 | 0 | 0
3.925 | 6.862 | 1.02
0 | 0 | 0
−10.17 | −7.92 | −11.51
0 | 0 | 0
−11.38 | 6.901 | 6.871
0 | 0 | 0
−2.231 −13.96 | 8.24

(4.26)

This shows that a model based on a decoupled system is a very strong limitation and only feasible at an operating point where all states are near zero. A fully operating ballbot with high dynamics can solely be based on a system that considers coupling effects.

3D System Modeling and Control | 4.4 Development of a 3D Model Based Controller

### 4.4 Development of a 3D Model Based Controller

As in chapter 2.4.2 above, a model based, linear full state-feedback LQR controller is proposed. Based on the linearized system with all operating points at zero, the following parameters for Q and R are chosen:

Q = diag (100, 50, 100, 50, 40, 20, 20, 10, 20, 10)

R = diag (100, 100, 100)

The values for Q are chosen similarly to the parameters described in section 2.4.2. R is chosen at a value so that during normal operation the input of the motors do not reach their limits.
The values in Q for ϑz and ϑ˙
z can be chosen without influencing the resulting gains for the other dynamics. They are chosen in a way, where at normal operation and disturbances, the ball does not start to slip about the vertical axis.
As an example, the resulting matrix K for the position control is given:

K =

22.34 | 4.63 | −0.00 | −0.00 −0.36 −0.29 | 0.36 | 0.53 | −0.00 −0.00
−11.17 −2.32 | 19.34 | 4.01 | −0.36 −0.29 −0.18 −0.26 | 0.31 | 0.46
−11.17 −2.32 −19.34 −4.01 −0.36 −0.29 −0.18 −0.26 −0.31 −0.46

### 4.5 Nonlinear Controller Design for the 3D Model

Considering the strong nonlinearities of the system (see 4.3.2), the next step is to develop

an appropriate nonlinear controller.

### 4.5.1 Concept

A suitable approach for a nonlinear controller is gain scheduling [8], regarding the size of the dynamic equations of the system (see 4.3.1). With that method, a linear controller

is designed at different operating points and the controller gains are interpolated for the current states during operation, i.e. combined to a nonlinear controller.
The nonlinear controller is developed for the velocity controller, because this is the mostly used controller by the different input generating projects. The states causing the systems nonlinearity are ϑx, ϑ˙
| | x, ϑy, ϑ˙

y, ϑ˙
z, ϕẋ, ϕ˙ y, u1, u2 and u3 while ϑx, ϑy, ϕẋ and ϕ˙ y having the strongest influence.
In order to design a full nonlinear controller, the 24 entries of the velocity state feedback controller matrix K have to be interpolated in these 10 dimensions. With a discretization of only five linearization points per state, the controller look up table contains 5

10

- 24 ≈ 23.4 · 10⁷
terms (curse of dimensionality).

4.5 Nonlinear Controller Design for the 3D Model | 3D System Modeling and Control

### 4.5.2 Implementation

Implementing this controller on the given processor [9] means that this number of terms

has to be decreased drastically because of memory and computational power limitations. Therefore, as a first approach, the focus was set on the non-linearities resulting from the velocity of the ballbot.
The primary issue with the linear controller in real tests is its incapability to control ϑz at high speeds, meaning over ∼2 m/s. At this speed, the ballbot can start oscillating

heavily about the inertial z-axis which can lead to an instability of the whole system. This effect can also be observed in the simulation illustrated with the plot on the left side of figure 4.7. The set points are a steep ramp for the velocity in y-direction from 0 to 2 m/s and a flat ramp for ϑz. Additionally, little disturbances are given for

ϕy. The right side of figure 4.7 shows that a nonlinear controller, based on linearization points for ϕẋ and ϕ˙ y, is able to ensure system stability while following the set points. The same nonlinear control as shown is implemented on the real system and initial tests have proved, that the controller works as expected. However, an elaborate analysis has

yet to be done.; time [s]; x dot [rad/s]; velocity input; model setpoint; y dot [rad/s]; "z [rad]; !x dot [rad/s]; !y dot [rad/s]

Figure 4.7: Performance of the linear (left) and the nonlinear controller (right) for the same set points

Simulation and Verification of the 3D Model

## 5 Simulation and Verification of the 3D Model

### 5.1 Implementation in Simulink

Similar to the planar model, the 3d model is also implemented in Simulink. However, the main difference is the way of implementation. Because of the size of the equations of motion, the model is implemented as S-function, which is optimized to make a real time simulation possible. All other functions are, whenever possible, implemented as MATLAB-functions. The advantage of this method is that the MATLAB-functions in the simulation are very similar to the C-functions in the real system. Therefore changes made in the simulation are transferred to the ballbot fast and with a low risk of migration errors.

VR Sink

Bot.translation

Pendl_z.rotation

Pendl_y.rotation

Pendl_x.rotation

Wheel1.rotation

Wheel2.rotation

Wheel3.rotation

Sphere.rotation

states | time torque

Setpoint Generator

r

Setpoint Filter

soll

ist

SOLL

Saturation

Plant

Odometry

States Odometry Data

Noise

S S_N

Conversion

States

Odometry Data

position

z_rotation

y_rotation

x_rotation

ow1_rotation

ow2_rotation

ow3_rotation

ball_rotation
Controller

r

States

u

Clock

u | States

r

u

r

Figure 5.1: Block schematic of the 3d simulation environment in Simulink

### 5.2 Verification of the 3D Model

Figure 5.2 shows the responses of the real system and the simulation of the model to a step on the position. The set point step on ϕx from 4 rad to -8 rad corresponds to a position difference of 1.5 m. The agreement of the step responses generally meet the expectations. The small deviations between the measured data and the simulated data are explained with the fact that the real system is not able to stand perfectly in place. The controller used for this experiment is based on the 3d model, and is able to achieve a very good performance. Therefore the model is a reasonable representation of the system.

5.2 Verification of the 3D Model | Simulation and Verification of the 3D Model

time [s]; x [rad]; position step; real sytem; model setpoint

Figure 5.2: System and model response on a position step from 4 rad to -8 rad and backwards

Contrary to the planar model, figure 5.3 shows the coupling effects occurring in the 3d model. Driving in x direction and then turning about the z-axis does now affect the motion in y direction, although there is no set point.

0 | 2 | 4 | 6 | 8 | 10 | 12 | 14 | 16 | 18 | 20

−4

−2

0

2

time [s]

φ

## x dot [rad/s]

velocity step

model
| setpoint
0 | 2 | 4 | 6 | 8 | 10 | 12 | 14 | 16 | 18 | 20

−20

−10

0

10

time [s]

φ

## y dot [rad/s]

0 | 2 | 4 | 6 | 8 | 10 | 12 | 14 | 16 | 18 | 20

−2

0

2

4

time [s]

θ

z [rad]

Figure 5.3: Response of the model on a velocity step in x direction (center) and a ramp on the rotation around the z-axis (bottom).

Simulation and Verification of the 3D Model | 5.2 Verification of the 3D Model

The setting of more complex set points, generated with a joystick, shows that the
agreement of the real system and the simulation is still good (fig. 5.4). Again, the

coupling effects are well recognizable. Further plots are shown in the appendix F.2.

time [s]; !z [rad]; rotation about z; real sytem; 3d model setpoint; !x dot [rad/s]; velocity x; real sytem 3d model setpoint; y dot [rad/s]; velocity y

Figure 5.4: System and model response on set points generated by a joystick

5.3 Comparison | Simulation and Verification of the 3D Model

### 5.3 Comparison

The main difference between the planar and the 3d model that affects the dynamics of the system are the couplings between the different axes. As already discussed in sections 3.6 and 5.2, this difference can be demonstrated easily. In figure 5.5, simulating the 3d model with the planar controller shows that this controller is not able to manage the couplings when driving at faster speed. Therefore the planar controller is not capable of performing complicated sequences of motion.

0 | 2 | 4 | 6 | 8 | 10 | 12 | 14 | 16 | 18 | 20

−20

0

20

time [s]

φ

## x dot [rad/s]

velocity step

model
setpoint
0 | 2 | 4 | 6 | 8 | 10 | 12 | 14 | 16 | 18 | 20

−20

−10

0

10

time [s]

φ

## y dot [rad/s]

0 | 2 | 4 | 6 | 8 | 10 | 12 | 14 | 16 | 18 | 20

0

2

4

time [s]

θ

z [rad]

Figure 5.5: System response of the 3d model stabilized by the the planar controller

Figure 5.6 shows that the planar controller is not able to follow the complex set points generated by a joystick. When driving at relatively high speed and then turning around the z-axis the system starts oscillating.

Simulation and Verification of the 3D Model; 5.3 Comparison; time [s]; !z [rad]; rotation about z; !x dot [rad/s]; velocity x; !y dot [rad/s]; velocity y

3d model with 2d controller
3d model
setpoint

Figure 5.6: Comparison of the system responses of the 3d model with the planar and the 3d controller

for set points generated by a joystick

Performance Analysis

## 6 Performance Analysis

During various tests, the performance of the controller was analyzed. Tests were performed on different coverings. Due to the additional damping and contact friction on carpets, the performance is slightly better than on hard floors.
Figure 6.1 shows the motion of the ballbot while balancing on a single point. For this test a special controller is used which contains a low pass filter on the controller output and therefore allows stronger gains. The maximum deviation from the initial point is 1 mm, compared to 20 mm, which is what other ballbots are capable of ([12],[7]).

position x [mm]; position y [mm]; standing in position

Figure 6.1: Deviation of the position for standing on a single point for 20 s

Greater differences between Rezero and other ballbots are shown in the following plots.

Figure 6.2 shows the maximum speed that was reached with the prototype. This test was performed with an angular controller which stabilizes only the angle and does not include position or speed (view section 2.4). The plot shows the rotation speed of the ball in rad/s. Converting to a speed in m/s by multiplying with the radius of the ball yields a maximum speed of 3.5 m/s.
The maximum tilt angle reached so far is 17◦
. The tilt angle corresponds directly to the acceleration of the ballbot. Compared to already existing ballbots ([12],[7]), this angle

is much bigger and shows the performance capability of the system and the controller. Figure 6.4 shows a picture of the prototype while tilting 17◦
. This test was done by
generating velocity set points with a joystick.

Performance Analysis; time [s]; speed; !x [rad]; tilt angle; motor torque; torque motor 2 [Nm]

absolute speed [rad/s]

Figure 6.2: Speed during speed test reaching its maximum at 3.5 m/s

torque motor 1 [Nm]

torque motor 3 [Nm]

Figure 6.3: Maximum tilt angle (left) and corresponding motor torques (right) during system test

The described performance analysis tests were done with the linear controller derived
from the 3d model. As the nonlinear controller shows promising potential (4.5), higher
performance by using a nonlinear controller can be assumed.

Performance Analysis


Figure 6.4: Performance demonstration, tilt angle of 17◦

Implementation

## 7 Implementation

### 7.1 Set Point Filter

To ensure that the set point jumps are feasible for the controller, the inputs generated by any input device are filtered by a set point filter. This filter makes a ramp from every input and limits its maximum (fig. 7.1). Consequently it has two tuning parameters: the

maximum inclination of the ramp and the maximum allowed input. The filter works the way, that if the set point difference is higher than the maximum allowed difference, the allowed difference is added to the last set point in the direction of the demanded set point. This is done every time before the set points are sent to the controller.
The inclination of the ramp is chosen at a value at which the torque of the motors just reach the their limits. The maximum velocity is limited to a value at which the linear controller is sufficient to stabilize the system (cf. section 4.5).

### velocity y

Figure 7.1: Raw set point and filtered value of the set point filter

Implementation | 7.2 Programming

### 7.2 Programming

The controller is implemented on a microcontroller running at 157.8 Hz. This control rate being sufficiently high, discrete control theory can be omitted and the continuous controller designed for the simulation is directly ported. The controller and all calculations are written in C-code.

## Torque conversion

## Controller

## Plant

## Helios

rK sin; Odometry; LQR; Encoders; x_position; IMU

Figure 7.2: Structure of the implemented control system

Figure 7.2 shows an overview of the implemented control structure for the planar controller. The states of the plant are measured by the IMU and the encoder of the motors. The latter have to be converted with the odometry in order to match the states from the controller. Accounting for the set point, this dataset is processed by the controller and converted in the torque conversion to deliver the appropriate set point for the motor controllers.
Integration for ϕx, ϕy and ϕz is realized as numerical integration in trapezoidal form. Further details of the software and electronics are described in [11] and [9].

### 7.3 Safety System

In system verification and performance tests, the physical ballbot prototype must be operated extensively. In order to avoid system damage and human injury, safety is a very important aspect of running a ballbot.
At system tests with unknown outcome, the ballbot is secured from falling on the ground with a specially designed, rollable safety frame. A emergency button is attached to the safety frame, enabling the operator to turn off the system immediately at any time. The motors are very powerful and capable of destroying the omniwheels or the ball. By limiting the maximum torques between 1.2 to 5 Nm, according to the situation, a harm

7.3 Safety System | Implementation

of equipment can be avoided. Also, to protect the gear heads, the motors are shut down as soon as they would accidentally rotate faster than at 8000 rpm.
Since the motors are limited to 5 Nm, the ballbot cannot stabilize tilting angles bigger
than ∼20◦ | . Running in a situation where the tilting angle exceeds this limit, the system
is turned off at 25◦
in order to prevent further damage.

Conclusion

## 8 Conclusion

This thesis has followed the goal of developing a controller for a highly agile and maneuverable ballbot. By relying on a simplified planar model first, a real-time simulation with a graphical user interface and three-dimensional visualization is developed. In order to control the real prototype, conversions for torques, moments of inertia and the odometry are calculated. A set of controllers for different inputs such as position, velocity and tilt angle are implemented. Advancing the system model, a full three-dimensional model is proposed and verified. A controller based on the 3d system is developed and shown to be able to stabilize the system for complex trajectories. Various experiments demonstrate the unique capabilities of the ballbot stabilized by the 3d controller. A nonlinear controller is proposed in order to expand the performance of the ballbot prototype.

### 8.1 Achievements

This thesis accomplishes the given goals and meets the requirements in agreement with other projects. At a very early stage, a working simulation has been developed and a controller implemented, stabilizing the real system. By advancing the system model in three dimensions and constant refining of the prototype, a unique controller has been successfully developed. With this controller, Rezero is the first ballbot to show the full potential of moving on a single ball. Rezero was presented in public for several times (see figure 8.1) and drew attention of many automation and control experts.

Having taken a step further, a nonlinear controller was proposed and shown to be more capable of stabilizing the system in high performance situations.

### 8.2 Prospect

The controller is able to push the system to its electrical and mechanical limitations in many respects. However, some desirable performance goals can be solved in a future work. For example, in a remote controlled mode, the speed limit is set to about 2 m/s

at the moment, which could be improved by implementing a nonlinear controller. Also, the system is very sensitive to noise and gear backlash. The motion precision could be improved by implementing a sophisticated filter like a Kalman filter and by replacing hardware elements, such as installing harmonic drives instead of planetary gears. Finally, very interesting problems like an adaptive control for automatic IMU calibration, variable payloads and slopes could be solved.

8.3 Personal Statement | Conclusion


Figure 8.1: Demonstration at Automatica in Munich

### 8.3 Personal Statement

This work on the modeling and control of our ballbot was a very interesting and educational journey to us. Based on a totally new and self constructed system, it is extremely rewarding to bring a system to life and develop the performance from the first trembling steps to a fast, flexible and robust system.
We think this thesis was a very worthy experience in many respects and we hope that the results will help the further development of Rezero and other ballbots.

Bibliography | Bibliography
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

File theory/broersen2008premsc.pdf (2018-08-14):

# University of Twente

# EEMCS / Electrical Engineering

## Control Engineering

# Enhancement of the masterclass robot

## Jeroen Broersen

### Individual Design Assignment

Supervisors:
prof.dr.ir. P.P.L. Regtien ir. E.C. Dertien

May 2008

Report nr. 009CE2008
Control Engineering
EE-Math-CS
University of Twente
P.O.Box 217
7500 AE Enschede
The Netherlands

# Summary

The masterclass robot is an educational robotplatform for showing students of secondary education the possibilities of robotics. At this moment the robot has proximity sensors and sensors for line following. To make it more challenging for the students it would be nice if the possibilities of the robot where enhanced in such a way that a group of robots can communicate together and know the location of each robot with respect to the others. This report describes the research to the possible enhancements of the robot. The conclusion is that there are good and easy to use modules for RF communication. For the position detection there are possibilities to use infrared, but there are no easy to use modules available.

Control Engineering | i
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

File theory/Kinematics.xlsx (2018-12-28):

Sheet: Kinematix
Kinematix |  |  |  |  |  |  | Inverse Kinematics
q | 45 ° | Angle between horzontal and one wheel
 | 0.090 m | radius of ball
 | 0.035 m | radius of wheel
dT | 0.004 s | time since last measurement
current absolute Map position
 | 1000 mm | absolute x-position on map
 | 1000 mm | absolute y-position on map
 | 50 mm | absolute movement along x
 | 0 mm | absolute movement along y
 | 10.0 °/s | angular velocity around z
Position in IMU coord-system
d | 0.040 ° | angle within last dT
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

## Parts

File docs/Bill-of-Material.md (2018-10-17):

## Components

|Category |  #| What | | Supplier |
|:---|--:|:---|:---|:---|
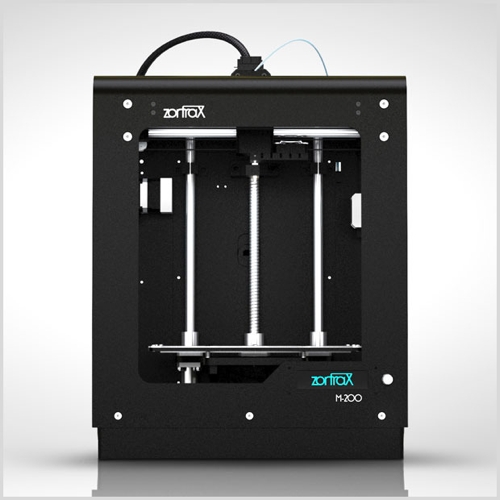
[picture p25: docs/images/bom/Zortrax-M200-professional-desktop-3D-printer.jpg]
|3D Print | 1 | ABS 3D printer |  | [Zortrax M200](https://store.zortrax.com/M200) |
| | | Petroleum, Acetone |  | Local Dealer | 																																			 |
|Electronics | 1 | NodeMCU V2, ESP8266 board |  |  [NodeMCU V2](https://www.seeedstudio.com/NodeMCU-v2-Lua-based-ESP8266-development-kit-p-2415.html) |
| | 1 | Teensy 3.5, Arm M4 board |  | [Teensy 3.5](https://www.pjrc.com/store/teensy35.html ) |
|3x Omniwheel |  | | | |
| |  | 2-component epoxy glue with 15 minutes set time (enough for one omniwheel) |  | [Epoxy30](https://www.amazon.de/Minuten-Epoxy-Kleber-Transparent-100/dp/B00MKAW3DA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) |
| |  | instant adhesive for porose surfaces |  | [Loctite 401](http://www.loctite.de/produktsuche-29727.htm?nodeid=8802625323009) |
| |  | Corundum (sharp-edged), 5kg, 0.15-0.2mm grain size |   |[Corundum 0.15-0.2mm](https://www.ebay.de/itm/Strahlmittel-Glasperlen-Korund-Schlacke-Granatsand-Strahlgut-Sandstrahlen/172177067505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) | 
| |3x24|Ball bearing 2x5x2.3 |  | [Deep grove ball bearing 2x5x2](https://www.kugellager-express.de/miniatur-kugellager-682-zz-2x5x2-3-mm) |
| |3x1| Mounting Hub for OmniWheel |  | [Mounting Hub for 4mm shaft](https://www.pololu.com/product/1997) |
| |3x4| Allen screws M3, 8mm length, DIN 912 |  | local dealer |
| |3x6| AllenScrews M2, 8mm length, DIN 912 |  | local dealer |
| |3x6| Screw Nut M2 DIN 934 |  | local dealer |
|3x drive chain |3x4| Allen screws M3, 8mm length, DIN 912, gear to mounting hub |  
| |3x3| Allen screws motor holder M2, 16mm length, DIN 912, motorholder to enclosure  |  |
| |3  | steel axis omniwheel 4mm, 39mm |  | local dealer | | |
| |3  | steel axis gear 4mm, 45mm |  | local dealer | | |
| |3x2| ball bearing motor pinion 4x7x2.5 |   | [Deep grove ball bearing 2x5x2](https://www.kugellager-express.de/miniatur-kugellager-mr74-zz-4x7x2-5-mm) |
| |3x3| ball bearing gear box 4x8x3 |   | [Deep grove ball bearing 2x5x2](https://www.kugellager-express.de/miniatur-kugellager-mr84-2rs-4x8x3-mm) |
| |3x2| Timing Belt for drive chain T2.5, 64 teeth, 160mm |   | [Timing Belt T2.5 160mm](https://www.keilriemenexpress.de/zahnflachriemen-zahnriemen-shop/synchroflex-zahnriemen-t/zahnriemen-t-2-5/zahnflachriemen-t-2-5-6-mm-breite/t2-5-160-mm-breite-6-mm.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) |

## Sources

|Category |  Description | Source |
|:---|:---|:---|
|CAD Model | Inventor model of all 3D parts | [Github Ondine CAD](https://github.com/jochenalt/ondine/tree/master/CAD) |
| | 3D printable files of body and legs parts | [Github Ondine STL](https://github.com/jochenalt/ondine/tree/master/stl) |
|Electronics | Eagle Schematics and PCBs | [Github Schematics](https://github.com/jochenalt/ondine/tree/master/schematics) |
|Source Code | C++ code running on Teensy 3.5 		 | [Github BotController](https://github.com/jochenalt/ondine/tree/master/code/BotController) |

## Tools
|Category |  Description | Source |
|:---|:---|:---|
|IDE for Teensy and ESP8266 | Eclipse derivate to develop and deploy in C++ on Teensy and n NodeMCU V2 |  [Eclipse Sloeber](http://eclipse.baeyens.it) |

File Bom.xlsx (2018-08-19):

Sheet: BOM
# | What | What for | Source
3 | Omni Wheels
1 | 2K Epoxy30 Glue | glue corundum to omniwheel roll | https://www.amazon.de/gp/product/B00XHR7RGS/ref=oh_aui_detailpage_o00_s00?ie=UTF8&psc=1
1 | Corundum (sharp-edged), 5kg, 0.15-0.2mm grain size | Friction surface of Omniwheels | https://www.ebay.de/itm/Strahlmittel-Glasperlen-Korund-Schlacke-Granatsand-Strahlgut-Sandstrahlen/172177067505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
72 | Ball bearing 2x5x2.0 | Omniwheel bearings | https://www.kugellager-express.de/miniatur-kugellager-682-zz-2x5x2-3-mm
3 | Mounting Hub for 4mm axis | Mounting hub OmniWheel | https://www.pololu.com/product/1997
4 | AllenScrews M3, 8mm length, DIN 912 | screw mounting hub to Omniwheel | https://www.ebay.de/itm/Zylinderschrauben-M2-M12-DIN-912-Edelstahl-A2-VA-V2A-Zylinderkopf-Innensechskant/272073684666
6 | AllenScrews M2, 8mm length, DIN 912 | screw mounting hub to Omniwheel | https://www.ebay.de/itm/Zylinderschrauben-M2-M12-DIN-912-Edelstahl-A2-VA-V2A-Zylinderkopf-Innensechskant/272073684666
3 | Mounting Hub for 4mm axis | Mounting hub for drive chain | https://www.pololu.com/product/1997
6 | Screw Nut M2 DIN 934 | Mounting OmniWheel to Mounting Hub | https://www.ebay.de/itm/Sechskantmuttern-DIN-934-Sechskant-Mutter-Muttern-M2-M33-8-8-Stahl-verzinkt-/282200543992
3 | Drive Chain
1 | Pololu DC motor Driver 5A peak | Driver for enclosure lifting motor | https://www.pololu.com/product/1212
1 | Pololu DC motor with Encoder 20.4:1, 5A, 0.6 Nm, 500RPM | Motor for lifting the enclosure | https://www.pololu.com/product/3215
2 | Axis 2mm, 500mm | Axis for Omniwheel rolls | https://www.conrad.de/de/silberstahl-welle-reely-o-x-l-2-mm-x-500-mm-237213.html | 1 | 2 | 2.34 € | 4.68 € | 0
1 | Axis 4mm, 500mm | Axis for Omniwheel hub | https://www.conrad.de/de/silberstahl-welle-reely-o-x-l-2-mm-x-500-mm-237213.html | 1 | 1 | 2.59 € | 2.59 € | 0
3 | Optical Encoder 1024 CPR | Omniwheel Encoder | https://www.mouser.de/ProductDetail/Broadcom-Avago/HEDM-5500J12?qs=RuhU64sK2%252bvlCf%252bZbiBtGg%3D%3D | 1 | 3 | 19.90 € | 59.70 € | 0
3 | Optical Encoder 300 CPR | Motor Encoder | https://www.robotshop.com/de/de/optischer-drehgeber-hkt22.html#
3 | BLDC Maxxon Motor with Hall sensors, 40W | Omniwheel motors | https://www.maxonmotor.com/maxon/view/product/272768 | 5 | 0 | 23.00 € | 0.00 € | 5
9 | Bearing 4x13x6 | PlanetaryGear Bearing | https://www.kugellager-express.de/miniatur-kugellager-626-2rs-6x19x6-mm | 1 | 5 | 1.00 € | 5.00 € | 4
9 | Allen screw DIN912 M2 | Planetary Bearing screw | https://www.schraubenkasten.de/schrauben/zylinderschrauben/din-912-mit-innensechskant/m2-din-912-12-9-stahl-zylinderschrauben-mit-innensechskant-blank/a-200192/ | 100 | 1 | 3.00 € | 3.00 € | 0
9 | Bearing 4x13x6 | OmniWheel Axis Bearings | https://www.kugellager-express.de/miniatur-kugellager-624-2rs-4x13x5-mm | 1 | 3 | 1.00 € | 3.00 € | 6
18 | Bearing 12x18x4 | Cycloid Gear Bearing | https://www.kugellager-express.de/rillenkugellager-6701-2rs-61701-2rs-12x18x4-mm | 1 | 18 | 1.34 € | 24.12 € | 0
4 | Bearing 4x7x2,5 | Cycloid Gear Bearing | https://www.kugellager-express.de/miniatur-kugellager-mr74-zz-4x7x2-5-mm | 1 | 4 | 1.19 € | 4.76 € | 0
9 | Reduzierhülsen 5mm 4mm | Reduzierhülse for Belt pulleys | https://spinblades.com/Reduzierhuelsen-5mm-4mm_1 | 1 | 1 | 0.90 € | 0.90 € | 0
3 | Brushless Motor Driver | Triple half bridge brushless motor driver | https://drotek.com/shop/en/home/212-brushless-gimbal-controller-l6234.html
3 | Molex Mini-Fit Jr 2x2 Socket | motor Socket | https://www.reichelt.de/molex-stiftleiste-mini-fit-jr-2x2-polig-stecker-molex-39288040-p190293.html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
3 | Molex Micro-Fit 3.0 TM 2x3 Socket | Hall Socket | https://www.reichelt.de/molex-stiftleiste-micro-fit-2x3-polig-stecker-molex-430450612-p186168.html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
 |  |  |  |  |  |  | 106.85 €
Material |  |  |  | Pieces in Pack | Packs to order | Price | Sum | Pieces in Stock
1 | 2K Epoxy30 Glue |  | https://www.amazon.de/gp/product/B00XHR7RGS/ref=oh_aui_detailpage_o00_s00?ie=UTF8&psc=1 | 1 | 0 | 19.90 € | 0.00 € | 1
1 | Corundum (sharp-edged), 5kg, 0.15-0.2mm grain size |  | https://www.ebay.de/itm/Strahlmittel-Glasperlen-Korund-Schlacke-Granatsand-Strahlgut-Sandstrahlen/172177067505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 | 1 | 0 | 19.90 € | 0.00 € | 1
72 | Ball bearing 2x5x2.0 |  | https://www.kugellager-express.de/miniatur-kugellager-682-zz-2x5x2-3-mm | 1 | 0 | 0.81 € | 0.00 € | 72
4 | AllenScrews M3, 8mm length, DIN 912 |  | https://www.ebay.de/itm/Zylinderschrauben-M2-M12-DIN-912-Edelstahl-A2-VA-V2A-Zylinderkopf-Innensechskant/272073684666 | 50 | 1 | 3.50 € | 3.50 € | 0
6 | AllenScrews M2, 8mm length, DIN 912 |  | https://www.ebay.de/itm/Zylinderschrauben-M2-M12-DIN-912-Edelstahl-A2-VA-V2A-Zylinderkopf-Innensechskant/272073684666 | 50 | 1 | 2.50 € | 2.50 €
6 | Mounting Hub for 4mm axis |  | https://www.pololu.com/product/1997 | 50 | 1 | 2.50 € | 2.50 €
6 | Screw Nut M2 DIN 934 |  | https://www.ebay.de/itm/Sechskantmuttern-DIN-934-Sechskant-Mutter-Muttern-M2-M33-8-8-Stahl-verzinkt-/282200543992 | 50 | 1 | 2.50 € | 2.50 € | 0
1 | Pololu DC motor Driver 5A peak |  | https://www.pololu.com/product/1212 | 1 | 1 | 16.00 € | 16.00 €
1 | Pololu DC motor with Encoder 20.4:1, 5A, 0.6 Nm, 500RPM |  | https://www.pololu.com/product/3215 | 1 | 1 | 40.00 € | 40.00 €

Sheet: DIN
Kugelkopf M3 2 mm Duraluminium

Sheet: RAL-Basic
1000 | Green beige | 204 204 153
 |  | CCCC99
1001 | Beige | 210 170 90
 |  | D2AA5A
1002 | Sand yellow | 208 168 24
 |  | D0A818
1003 | Signal yellow | 255 204 0
 |  | FFCC00
1004 | Golden yellow | 224 176 0
 |  | E0B000
1005 | Honey yellow | 201 135 33
 |  | C98721
1006 | Maize yellow | 227 167 41
 |  | E3A729
1007 | Daffodil yellow | 221 159 35
 |  | DD9F23
1011 | Brown beige | 173 122 41
 |  | AD7A29
1012 | Lemon yellow | 227 184 56
 |  | E3B838
1013 | Oyster white | 255 245 227
 |  | FFF5E3
1014 | Ivory | 240 214 171
 |  | F0D6AB
1015 | Light ivory | 252 235 204
 |  | FCEBCC
1016 | Sulfur yellow | 255 245 66
 |  | FFF542
1017 | Saffron yellow | 255 171 89
 |  | FFAB59
1018 | Zinc yellow | 255 214 77
 |  | FFD64D
1019 | Grey beige | 163 140 122
 |  | A38C7A
1020 | Olive yellow | 156 143 97
 |  | 9C8F61
1021 | Rape yellow | 252 189 31
 |  | FCBD1F
1023 | Traffic yellow | 252 189 31
 |  | FCBD1F
1024 | Ochre yellow | 181 140 79
 |  | B58C4F
1026 | Luminous yellow | 255 255 10
 |  | FFFF0A
1027 | Curry | 153 117 33
 |  | 997521
1028 | Melon yellow | 255 140 26
 |  | FF8C1A
1032 | Broom yellow | 227 163 41
 |  | E3A329
1033 | Dahlia yellow | 255 148 54
 |  | FF9436
1034 | Pastel yellow | 247 153 92
 |  | F7995C
2000 | Yellow orange | 224 94 31
 |  | E05E1F
2001 | Red orange | 186 46 33
 |  | BA2E21
2002 | Vermilion | 204 36 28
 |  | CC241C
2003 | Pastel orange | 255 99 54
 |  | FF6336
2004 | Pure orange | 242 59 28
 |  | F23B1C
2005 | Luminous orange | 252 28 20
 |  | FC1C14
2007 | Luminous bright orange | 255 117 33
 |  | FF7521
2008 | Bright red orange | 250 79 41
 |  | FA4F29
2009 | Traffic orange | 235 59 28
 |  | EB3B1C
2010 | Signal orange | 212 69 41
 |  | D44529
2011 | Deep orange | 237 92 0
 |  | ED5C00
2012 | Salmon orange | 222 82 71
 |  | DE5247
3000 | Flame red | 171 31 28
 |  | AB1F1C
3001 | Signal red | 163 23 26
 |  | A3171A
3002 | Carmine red | 163 26 26
 |  | A31A1A
3003 | Ruby red | 138 18 20
 |  | 8A1214
3004 | Purple red | 105 15 20
 |  | 690F14
3005 | Wine red | 79 18 26
 |  | 4F121A
3007 | Black red | 46 18 26
 |  | 2E121A
3009 | Oxide red | 94 33 33
 |  | 5E2121
3011 | Brown red | 120 20 23
 |  | 781417
3012 | Beige red | 204 130 115
 |  | CC8273
3013 | Tomato red | 150 31 28
 |  | 961F1C
3014 | Antique pink | 217 102 117
 |  | D96675
3015 | Light pink | 232 156 181
 |  | E89CB5
3016 | Coral red | 166 36 38
 |  | A62426
3017 | Rose | 209 54 84
 |  | D13654
3018 | Strawberry red | 207 41 66
 |  | CF2942
3020 | Traffic red | 199 23 18
 |  | C71712
3022 | Salmon pink | 217 89 79
 |  | D9594F
3024 | Luminous red | 252 10 28
 |  | FC0A1C
3026 | Luminous bright red | 252 20 20
 |  | FC1414
3027 | Raspberry red | 181 18 51
 |  | B51233
3031 | Orient red | 166 28 46
 |  | A61C2E
4001 | Red lilac | 130 64 48
 |  | 824030
4002 | Red violet | 143 38 64
 |  | 8F2640
4003 | Heather violet | 201 56 140
 |  | C9388C
4004 | Claret violet | 92 8 43
 |  | 5C082B
4005 | Blue lilac | 99 61 156
 |  | 633D9C
4006 | Traffic purple | 145 15 102
 |  | 910F66
4007 | Purple violet | 56 10 46
 |  | 380A2E
4008 | Signal violet | 125 31 122
 |  | 7D1F7A
4009 | Pastel violet | 158 115 148
 |  | 9E7394
4010 | Telemagenta | 191 23 115
 |  | BF1773
5000 | Violet blue | 23 51 107
 |  | 17336B
5001 | Green blue | 10 51 84
 |  | 0A3354
5002 | Ultramarine blue | 0 15 117
 |  | 000F75
5003 | Sapphire blue | 0 23 69
 |  | 001745
5004 | Black blue | 3 13 31
 |  | 030D1F
5005 | Signal blue | 0 46 122
 |  | 002E7A
5007 | Brillant blue | 38 79 135
 |  | 264F87
5008 | Gray blue | 26 41 56
 |  | 1A2938
5009 | Azure blue | 23 69 112
 |  | 174570
5011 | Steel blue | 0 43 112
 |  | 002B70
5012 | Light blue | 41 115 184
 |  | 2973B8
5013 | Cobalt blue | 0 18 69
 |  | 001245
5014 | Pigeon blue | 77 105 153
 |  | 4D6999
5015 | Sky blue | 23 97 171
 |  | 1761AB
5017 | Traffic blue | 0 59 128
 |  | 003B80
5018 | Turquoise blue | 56 148 130
 |  | 389482
5019 | Capri blue | 10 66 120
 |  | 0A4278
5020 | Steel blue | 5 51 51
 |  | 053333
5021 | Water blue | 26 122 99
 |  | 1A7A63
5022 | Night blue | 0 8 79
 |  | 00084F
5023 | Distant blue | 46 82 143
 |  | 2E528F
5024 | Pastel blue | 87 140 171
 |  | 578CAB
6000 | Patina green | 51 120 84
 |  | 337854
6001 | Emerald green | 38 102 81
 |  | 266651
6002 | Leaf green | 38 87 33
 |  | 265721
6003 | Olive green | 61 69 46
 |  | 3D452E
6004 | Blue green | 13 59 46
 |  | 0D3B2E
6005 | Moss green | 10 56 31
 |  | 0A381F
6006 | Grey olive | 41 43 46
 |  | 292B2E
6007 | Bottle green | 28 38 23
 |  | 1C2617
6008 | Brown green | 33 33 26
 |  | 21211A
6009 | Fir green | 23 41 28
 |  | 17291C
6010 | Grass green | 54 105 38
 |  | 366926
6011 | Reseda green | 94 125 79
 |  | 5E7D4F
6012 | Black green | 31 46 43
 |  | 1F2E2B
6013 | Reed green | 117 115 79
 |  | 75734F
6014 | Yellow olive | 51 48 38
 |  | 333026
6015 | Black olive | 41 43 38
 |  | 292B26
6016 | Turquoise green | 15 112 51
 |  | 0F7033
6017 | Yellow green | 64 130 54
 |  | 408236
6018 | May green | 79 168 51
 |  | 4FA833
6019 | Pastel green | 191 227 186
 |  | BFE3BA
6020 | Chrome green | 38 56 41
 |  | 263829
6021 | Pale green | 133 166 122
 |  | 85A67A
6022 | Olive drab | 43 38 28
 |  | 2B261C
6024 | Traffic green | 36 145 64
 |  | 249140
6025 | Fern green | 74 110 51
 |  | 4A6E33
6026 | Opal green | 10 92 51
 |  | 0A5C33
6027 | Light green | 125 204 189
 |  | 7DCCBD
6028 | Pine green | 38 74 51
 |  | 264A33
6029 | Mint green | 18 120 38
 |  | 127826
6032 | Signal green | 41 138 64
 |  | 298A40
6033 | Mint turquoise | 66 140 120
 |  | 428C78
6034 | Pastel turquoise | 125 189 181
 |  | 7DBDB5
7000 | Squirrel grey | 115 133 145
 |  | 738591
7001 | Silver grey | 135 148 166
 |  | 8794A6
7002 | Olive grey | 122 117 97
 |  | 7A7561
7003 | Moss grey | 112 112 97
 |  | 707061
7004 | Signal grey | 156 156 166
 |  | 9C9CA6
7005 | Mouse grey | 97 105 105
 |  | 616969
7006 | Beige grey | 107 97 87
 |  | 6B6157
7008 | Khaki grey | 105 84 56
 |  | 695438
7009 | Green grey | 77 82 74
 |  | 4D524A
7010 | Tarpaulin grey | 74 79 74
 |  | 4A4F4A
7011 | Iron grey | 64 74 84
 |  | 404A54
7012 | Basalt grey | 74 84 89
 |  | 4A5459
7013 | Brown grey | 71 66 56
 |  | 474238
7015 | Slate grey | 61 66 82
 |  | 3D4252
7016 | Anthracite grey | 38 46 56
 |  | 262E38
7021 | Black grey | 26 33 41
 |  | 1A2129
7022 | Umbra grey | 61 61 59
 |  | 3D3D3B
7023 | Concrete grey | 122 125 117
 |  | 7A7D75
7024 | Graphite grey | 48 56 69
 |  | 303845
7026 | Granite grey | 38 51 56
 |  | 263338
7030 | Stone grey | 145 143 135
 |  | 918F87
7031 | Blue grey | 77 92 107
 |  | 4D5C6B
7032 | Pebble grey | 189 186 171
 |  | BDBAAB
7033 | Cement grey | 122 130 117
 |  | 7A8275
7034 | Yellow grey | 143 135 112
 |  | 8F8770
7035 | Light grey | 212 217 219
 |  | D4D9DB
7036 | Platinum grey | 158 150 156
 |  | 9E969C
7037 | Dusty grey | 122 125 128
 |  | 7A7D80
7038 | Agate grey | 186 189 186
 |  | BABDBA
7039 | Quartz grey | 97 94 89
 |  | 615E59
7040 | Window grey | 158 163 176
 |  | 9EA3B0
7042 | Verkehrsgrau A | 143 150 153
 |  | 8F9699
7043 | Verkehrsgrau B | 64 69 69
 |  | 404545
7044 | Silk grey | 194 191 184
 |  | C2BFB8
7045 | Telegrau 1 | 143 148 158
 |  | 8F949E
7046 | Telegrau 2 | 120 130 140
 |  | 78828C
7047 | Telegrau 4 | 217 214 219
 |  | D9D6DB
8000 | Green brown | 125 92 56
 |  | 7D5C38
8001 | Ocher brown | 145 82 46
 |  | 91522E
8002 | Signal brown | 110 59 58
 |  | 6E3B3A
8003 | Clay brown | 115 59 36
 |  | 733B24
8004 | Copper brown | 133 56 43
 |  | 85382B
8007 | Fawn brown | 94 51 33
 |  | 5E3321
8008 | Olive brown | 99 61 36
 |  | 633D24
8011 | Nut brown | 71 38 28
 |  | 47261C
8012 | Red brown | 84 31 31
 |  | 541F1F
8014 | Sepia brown | 56 38 28
 |  | 38261C

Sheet: RAL
# | Name | Name | Name |  | Red | Blue | Green
1000 | Green beige | GreenBeige | GreenBeige | 204 204 153 | 204 | 204 | 153 | Green beige | #define GreenBeige ((204<<16) + ( 204<<8) + 153 )
1001 | Beige | Beige | Beige | 210 170 90 | 210 | 170 | 90 | Beige | #define Beige ((210<<16) + ( 170<<8) + 90 )
1002 | Sand yellow | SandYellow | SandYellow | 208 168 24 | 208 | 168 | 24 | Sand yellow | #define SandYellow ((208<<16) + ( 168<<8) + 24 )
1003 | Signal yellow | SignalYellow | SignalYellow | 255 204 0 | 255 | 204 | 0 | Signal yellow | #define SignalYellow ((255<<16) + ( 204<<8) + 0 )
1004 | Golden yellow | GoldenYellow | GoldenYellow | 224 176 0 | 224 | 176 | 0 | Golden yellow | #define GoldenYellow ((224<<16) + ( 176<<8) + 0 )
1005 | Honey yellow | HoneyYellow | HoneyYellow | 201 135 33 | 201 | 135 | 33 | Honey yellow | #define HoneyYellow ((201<<16) + ( 135<<8) + 33 )
1006 | Maize yellow | MaizeYellow | MaizeYellow | 227 167 41 | 227 | 167 | 41 | Maize yellow | #define MaizeYellow ((227<<16) + ( 167<<8) + 41 )
1007 | Daffodil yellow | DaffodilYellow | DaffodilYellow | 221 159 35 | 221 | 159 | 35 | Daffodil yellow | #define DaffodilYellow ((221<<16) + ( 159<<8) + 35 )
1011 | Brown beige | BrownBeige | BrownBeige | 173 122 41 | 173 | 122 | 41 | Brown beige | #define BrownBeige ((173<<16) + ( 122<<8) + 41 )
1012 | Lemon yellow | LemonYellow | LemonYellow | 227 184 56 | 227 | 184 | 56 | Lemon yellow | #define LemonYellow ((227<<16) + ( 184<<8) + 56 )
1013 | Oyster white | OysterWhite | OysterWhite | 255 245 227 | 255 | 245 | 227 | Oyster white | #define OysterWhite ((255<<16) + ( 245<<8) + 227 )
1014 | Ivory | Ivory | Ivory | 240 214 171 | 240 | 214 | 171 | Ivory | #define Ivory ((240<<16) + ( 214<<8) + 171 )
1015 | Light ivory | LightIvory | LightIvory | 252 235 204 | 252 | 235 | 204 | Light ivory | #define LightIvory ((252<<16) + ( 235<<8) + 204 )
1016 | Sulfur yellow | SulfurYellow | SulfurYellow | 255 245 66 | 255 | 245 | 66 | Sulfur yellow | #define SulfurYellow ((255<<16) + ( 245<<8) + 66 )
1017 | Saffron yellow | SaffronYellow | SaffronYellow | 255 171 89 | 255 | 171 | 89 | Saffron yellow | #define SaffronYellow ((255<<16) + ( 171<<8) + 89 )
1018 | Zinc yellow | ZincYellow | ZincYellow | 255 214 77 | 255 | 214 | 77 | Zinc yellow | #define ZincYellow ((255<<16) + ( 214<<8) + 77 )
1019 | Grey beige | GreyBeige | GreyBeige | 163 140 122 | 163 | 140 | 122 | Grey beige | #define GreyBeige ((163<<16) + ( 140<<8) + 122 )
1020 | Olive yellow | OliveYellow | OliveYellow | 156 143 97 | 156 | 143 | 97 | Olive yellow | #define OliveYellow ((156<<16) + ( 143<<8) + 97 )
1021 | Rape yellow | RapeYellow | RapeYellow | 252 189 31 | 252 | 189 | 31 | Rape yellow | #define RapeYellow ((252<<16) + ( 189<<8) + 31 )
1023 | Traffic yellow | TrafficYellow | TrafficYellow | 252 189 31 | 252 | 189 | 31 | Traffic yellow | #define TrafficYellow ((252<<16) + ( 189<<8) + 31 )
1024 | Ochre yellow | OchreYellow | OchreYellow | 181 140 79 | 181 | 140 | 79 | Ochre yellow | #define OchreYellow ((181<<16) + ( 140<<8) + 79 )
1026 | Luminous yellow | LuminousYellow | LuminousYellow | 255 255 10 | 255 | 255 | 10 | Luminous yellow | #define LuminousYellow ((255<<16) + ( 255<<8) + 10 )
1027 | Curry | Curry | Curry | 153 117 33 | 153 | 117 | 33 | Curry | #define Curry ((153<<16) + ( 117<<8) + 33 )
1028 | Melon yellow | MelonYellow | MelonYellow | 255 140 26 | 255 | 140 | 26 | Melon yellow | #define MelonYellow ((255<<16) + ( 140<<8) + 26 )
1032 | Broom yellow | BroomYellow | BroomYellow | 227 163 41 | 227 | 163 | 41 | Broom yellow | #define BroomYellow ((227<<16) + ( 163<<8) + 41 )
1033 | Dahlia yellow | DahliaYellow | DahliaYellow | 255 148 54 | 255 | 148 | 54 | Dahlia yellow | #define DahliaYellow ((255<<16) + ( 148<<8) + 54 )
1034 | Pastel yellow | PastelYellow | PastelYellow | 247 153 92 | 247 | 153 | 92 | Pastel yellow | #define PastelYellow ((247<<16) + ( 153<<8) + 92 )
2000 | Yellow orange | YellowOrange | YellowOrange | 224 94 31 | 224 | 94 | 31 | Yellow orange | #define YellowOrange ((224<<16) + ( 94<<8) + 31 )
2001 | Red orange | RedOrange | RedOrange | 186 46 33 | 186 | 46 | 33 | Red orange | #define RedOrange ((186<<16) + ( 46<<8) + 33 )
2002 | Vermilion | Vermilion | Vermilion | 204 36 28 | 204 | 36 | 28 | Vermilion | #define Vermilion ((204<<16) + ( 36<<8) + 28 )
2003 | Pastel orange | PastelOrange | PastelOrange | 255 99 54 | 255 | 99 | 54 | Pastel orange | #define PastelOrange ((255<<16) + ( 99<<8) + 54 )
2004 | Pure orange | PureOrange | PureOrange | 242 59 28 | 242 | 59 | 28 | Pure orange | #define PureOrange ((242<<16) + ( 59<<8) + 28 )
2005 | Luminous orange | LuminousOrange | LuminousOrange | 252 28 20 | 252 | 28 | 20 | Luminous orange | #define LuminousOrange ((252<<16) + ( 28<<8) + 20 )
2007 | Luminous bright orange | LuminousBright orange | LuminousBrightOrange | 255 117 33 | 255 | 117 | 33 | Luminous bright orange | #define LuminousBrightOrange ((255<<16) + ( 117<<8) + 33 )
2008 | Bright red orange | BrightRed orange | BrightRedOrange | 250 79 41 | 250 | 79 | 41 | Bright red orange | #define BrightRedOrange ((250<<16) + ( 79<<8) + 41 )
2009 | Traffic orange | TrafficOrange | TrafficOrange | 235 59 28 | 235 | 59 | 28 | Traffic orange | #define TrafficOrange ((235<<16) + ( 59<<8) + 28 )
2010 | Signal orange | SignalOrange | SignalOrange | 212 69 41 | 212 | 69 | 41 | Signal orange | #define SignalOrange ((212<<16) + ( 69<<8) + 41 )
2011 | Deep orange | DeepOrange | DeepOrange | 237 92 0 | 237 | 92 | 0 | Deep orange | #define DeepOrange ((237<<16) + ( 92<<8) + 0 )
2012 | Salmon orange | SalmonOrange | SalmonOrange | 222 82 71 | 222 | 82 | 71 | Salmon orange | #define SalmonOrange ((222<<16) + ( 82<<8) + 71 )
3000 | Flame red | FlameRed | FlameRed | 171 31 28 | 171 | 31 | 28 | Flame red | #define FlameRed ((171<<16) + ( 31<<8) + 28 )
3001 | Signal red | SignalRed | SignalRed | 163 23 26 | 163 | 23 | 26 | Signal red | #define SignalRed ((163<<16) + ( 23<<8) + 26 )
3002 | Carmine red | CarmineRed | CarmineRed | 163 26 26 | 163 | 26 | 26 | Carmine red | #define CarmineRed ((163<<16) + ( 26<<8) + 26 )
3003 | Ruby red | RubyRed | RubyRed | 138 18 20 | 138 | 18 | 20 | Ruby red | #define RubyRed ((138<<16) + ( 18<<8) + 20 )
3004 | Purple red | PurpleRed | PurpleRed | 105 15 20 | 105 | 15 | 20 | Purple red | #define PurpleRed ((105<<16) + ( 15<<8) + 20 )
3005 | Wine red | WineRed | WineRed | 79 18 26 | 79 | 18 | 26 | Wine red | #define WineRed ((79<<16) + ( 18<<8) + 26 )
3007 | Black red | BlackRed | BlackRed | 46 18 26 | 46 | 18 | 26 | Black red | #define BlackRed ((46<<16) + ( 18<<8) + 26 )
3009 | Oxide red | OxideRed | OxideRed | 94 33 33 | 94 | 33 | 33 | Oxide red | #define OxideRed ((94<<16) + ( 33<<8) + 33 )
3011 | Brown red | BrownRed | BrownRed | 120 20 23 | 120 | 20 | 23 | Brown red | #define BrownRed ((120<<16) + ( 20<<8) + 23 )
3012 | Beige red | BeigeRed | BeigeRed | 204 130 115 | 204 | 130 | 115 | Beige red | #define BeigeRed ((204<<16) + ( 130<<8) + 115 )
3013 | Tomato red | TomatoRed | TomatoRed | 150 31 28 | 150 | 31 | 28 | Tomato red | #define TomatoRed ((150<<16) + ( 31<<8) + 28 )
3014 | Antique pink | AntiquePink | AntiquePink | 217 102 117 | 217 | 102 | 117 | Antique pink | #define AntiquePink ((217<<16) + ( 102<<8) + 117 )
3015 | Light pink | LightPink | LightPink | 232 156 181 | 232 | 156 | 181 | Light pink | #define LightPink ((232<<16) + ( 156<<8) + 181 )
3016 | Coral red | CoralRed | CoralRed | 166 36 38 | 166 | 36 | 38 | Coral red | #define CoralRed ((166<<16) + ( 36<<8) + 38 )
3017 | Rose | Rose | Rose | 209 54 84 | 209 | 54 | 84 | Rose | #define Rose ((209<<16) + ( 54<<8) + 84 )
3018 | Strawberry red | StrawberryRed | StrawberryRed | 207 41 66 | 207 | 41 | 66 | Strawberry red | #define StrawberryRed ((207<<16) + ( 41<<8) + 66 )
3020 | Traffic red | TrafficRed | TrafficRed | 199 23 18 | 199 | 23 | 18 | Traffic red | #define TrafficRed ((199<<16) + ( 23<<8) + 18 )
3022 | Salmon pink | SalmonPink | SalmonPink | 217 89 79 | 217 | 89 | 79 | Salmon pink | #define SalmonPink ((217<<16) + ( 89<<8) + 79 )
3024 | Luminous red | LuminousRed | LuminousRed | 252 10 28 | 252 | 10 | 28 | Luminous red | #define LuminousRed ((252<<16) + ( 10<<8) + 28 )
3026 | Luminous bright red | LuminousBright red | LuminousBrightRed | 252 20 20 | 252 | 20 | 20 | Luminous bright red | #define LuminousBrightRed ((252<<16) + ( 20<<8) + 20 )
3027 | Raspberry red | RaspberryRed | RaspberryRed | 181 18 51 | 181 | 18 | 51 | Raspberry red | #define RaspberryRed ((181<<16) + ( 18<<8) + 51 )
3031 | Orient red | OrientRed | OrientRed | 166 28 46 | 166 | 28 | 46 | Orient red | #define OrientRed ((166<<16) + ( 28<<8) + 46 )
4001 | Red lilac | RedLilac | RedLilac | 130 64 48 | 130 | 64 | 48 | Red lilac | #define RedLilac ((130<<16) + ( 64<<8) + 48 )
4002 | Red violet | RedViolet | RedViolet | 143 38 64 | 143 | 38 | 64 | Red violet | #define RedViolet ((143<<16) + ( 38<<8) + 64 )
4003 | Heather violet | HeatherViolet | HeatherViolet | 201 56 140 | 201 | 56 | 140 | Heather violet | #define HeatherViolet ((201<<16) + ( 56<<8) + 140 )
4004 | Claret violet | ClaretViolet | ClaretViolet | 92 8 43 | 92 | 8 | 43 | Claret violet | #define ClaretViolet ((92<<16) + ( 8<<8) + 43 )
4005 | Blue lilac | BlueLilac | BlueLilac | 99 61 156 | 99 | 61 | 156 | Blue lilac | #define BlueLilac ((99<<16) + ( 61<<8) + 156 )
4006 | Traffic purple | TrafficPurple | TrafficPurple | 145 15 102 | 145 | 15 | 102 | Traffic purple | #define TrafficPurple ((145<<16) + ( 15<<8) + 102 )
4007 | Purple violet | PurpleViolet | PurpleViolet | 56 10 46 | 56 | 10 | 46 | Purple violet | #define PurpleViolet ((56<<16) + ( 10<<8) + 46 )
4008 | Signal violet | SignalViolet | SignalViolet | 125 31 122 | 125 | 31 | 122 | Signal violet | #define SignalViolet ((125<<16) + ( 31<<8) + 122 )
4009 | Pastel violet | PastelViolet | PastelViolet | 158 115 148 | 158 | 115 | 148 | Pastel violet | #define PastelViolet ((158<<16) + ( 115<<8) + 148 )
4010 | Telemagenta | Telemagenta | Telemagenta | 191 23 115 | 191 | 23 | 115 | Telemagenta | #define Telemagenta ((191<<16) + ( 23<<8) + 115 )
5000 | Violet blue | VioletBlue | VioletBlue | 23 51 107 | 23 | 51 | 107 | Violet blue | #define VioletBlue ((23<<16) + ( 51<<8) + 107 )
5001 | Green blue | GreenBlue | GreenBlue | 10 51 84 | 10 | 51 | 84 | Green blue | #define GreenBlue ((10<<16) + ( 51<<8) + 84 )
5002 | Ultramarine blue | UltramarineBlue | UltramarineBlue | 0 15 117 | 0 | 15 | 117 | Ultramarine blue | #define UltramarineBlue ((0<<16) + ( 15<<8) + 117 )
5003 | Sapphire blue | SapphireBlue | SapphireBlue | 0 23 69 | 0 | 23 | 69 | Sapphire blue | #define SapphireBlue ((0<<16) + ( 23<<8) + 69 )
5004 | Black blue | BlackBlue | BlackBlue | 3 13 31 | 3 | 13 | 31 | Black blue | #define BlackBlue ((3<<16) + ( 13<<8) + 31 )
5005 | Signal blue | SignalBlue | SignalBlue | 0 46 122 | 0 | 46 | 122 | Signal blue | #define SignalBlue ((0<<16) + ( 46<<8) + 122 )
5007 | Brillant blue | BrillantBlue | BrillantBlue | 38 79 135 | 38 | 79 | 135 | Brillant blue | #define BrillantBlue ((38<<16) + ( 79<<8) + 135 )
5008 | Gray blue | GrayBlue | GrayBlue | 26 41 56 | 26 | 41 | 56 | Gray blue | #define GrayBlue ((26<<16) + ( 41<<8) + 56 )
5009 | Azure blue | AzureBlue | AzureBlue | 23 69 112 | 23 | 69 | 112 | Azure blue | #define AzureBlue ((23<<16) + ( 69<<8) + 112 )
5011 | Steel blue | SteelBlue | SteelBlue | 0 43 112 | 0 | 43 | 112 | Steel blue | #define SteelBlue ((0<<16) + ( 43<<8) + 112 )
5012 | Light blue | LightBlue | LightBlue | 41 115 184 | 41 | 115 | 184 | Light blue | #define LightBlue ((41<<16) + ( 115<<8) + 184 )
5013 | Cobalt blue | CobaltBlue | CobaltBlue | 0 18 69 | 0 | 18 | 69 | Cobalt blue | #define CobaltBlue ((0<<16) + ( 18<<8) + 69 )
5014 | Pigeon blue | PigeonBlue | PigeonBlue | 77 105 153 | 77 | 105 | 153 | Pigeon blue | #define PigeonBlue ((77<<16) + ( 105<<8) + 153 )
5015 | Sky blue | SkyBlue | SkyBlue | 23 97 171 | 23 | 97 | 171 | Sky blue | #define SkyBlue ((23<<16) + ( 97<<8) + 171 )
5017 | Traffic blue | TrafficBlue | TrafficBlue | 0 59 128 | 0 | 59 | 128 | Traffic blue | #define TrafficBlue ((0<<16) + ( 59<<8) + 128 )
5018 | Turquoise blue | TurquoiseBlue | TurquoiseBlue | 56 148 130 | 56 | 148 | 130 | Turquoise blue | #define TurquoiseBlue ((56<<16) + ( 148<<8) + 130 )
5019 | Capri blue | CapriBlue | CapriBlue | 10 66 120 | 10 | 66 | 120 | Capri blue | #define CapriBlue ((10<<16) + ( 66<<8) + 120 )
5020 | Steel blue | SteelBlue | SteelBlue | 5 51 51 | 5 | 51 | 51 | Steel blue | #define SteelBlue ((5<<16) + ( 51<<8) + 51 )
5021 | Water blue | WaterBlue | WaterBlue | 26 122 99 | 26 | 122 | 99 | Water blue | #define WaterBlue ((26<<16) + ( 122<<8) + 99 )
5022 | Night blue | NightBlue | NightBlue | 0 8 79 | 0 | 8 | 79 | Night blue | #define NightBlue ((0<<16) + ( 8<<8) + 79 )
5023 | Distant blue | DistantBlue | DistantBlue | 46 82 143 | 46 | 82 | 143 | Distant blue | #define DistantBlue ((46<<16) + ( 82<<8) + 143 )
5024 | Pastel blue | PastelBlue | PastelBlue | 87 140 171 | 87 | 140 | 171 | Pastel blue | #define PastelBlue ((87<<16) + ( 140<<8) + 171 )
6000 | Patina green | PatinaGreen | PatinaGreen | 51 120 84 | 51 | 120 | 84 | Patina green | #define PatinaGreen ((51<<16) + ( 120<<8) + 84 )
6001 | Emerald green | EmeraldGreen | EmeraldGreen | 38 102 81 | 38 | 102 | 81 | Emerald green | #define EmeraldGreen ((38<<16) + ( 102<<8) + 81 )
6002 | Leaf green | LeafGreen | LeafGreen | 38 87 33 | 38 | 87 | 33 | Leaf green | #define LeafGreen ((38<<16) + ( 87<<8) + 33 )
6003 | Olive green | OliveGreen | OliveGreen | 61 69 46 | 61 | 69 | 46 | Olive green | #define OliveGreen ((61<<16) + ( 69<<8) + 46 )
6004 | Blue green | BlueGreen | BlueGreen | 13 59 46 | 13 | 59 | 46 | Blue green | #define BlueGreen ((13<<16) + ( 59<<8) + 46 )
6005 | Moss green | MossGreen | MossGreen | 10 56 31 | 10 | 56 | 31 | Moss green | #define MossGreen ((10<<16) + ( 56<<8) + 31 )
6006 | Grey olive | GreyOlive | GreyOlive | 41 43 46 | 41 | 43 | 46 | Grey olive | #define GreyOlive ((41<<16) + ( 43<<8) + 46 )
6007 | Bottle green | BottleGreen | BottleGreen | 28 38 23 | 28 | 38 | 23 | Bottle green | #define BottleGreen ((28<<16) + ( 38<<8) + 23 )
6008 | Brown green | BrownGreen | BrownGreen | 33 33 26 | 33 | 33 | 26 | Brown green | #define BrownGreen ((33<<16) + ( 33<<8) + 26 )
6009 | Fir green | FirGreen | FirGreen | 23 41 28 | 23 | 41 | 28 | Fir green | #define FirGreen ((23<<16) + ( 41<<8) + 28 )
6010 | Grass green | GrassGreen | GrassGreen | 54 105 38 | 54 | 105 | 38 | Grass green | #define GrassGreen ((54<<16) + ( 105<<8) + 38 )
6011 | Reseda green | ResedaGreen | ResedaGreen | 94 125 79 | 94 | 125 | 79 | Reseda green | #define ResedaGreen ((94<<16) + ( 125<<8) + 79 )
6012 | Black green | BlackGreen | BlackGreen | 31 46 43 | 31 | 46 | 43 | Black green | #define BlackGreen ((31<<16) + ( 46<<8) + 43 )
6013 | Reed green | ReedGreen | ReedGreen | 117 115 79 | 117 | 115 | 79 | Reed green | #define ReedGreen ((117<<16) + ( 115<<8) + 79 )
6014 | Yellow olive | YellowOlive | YellowOlive | 51 48 38 | 51 | 48 | 38 | Yellow olive | #define YellowOlive ((51<<16) + ( 48<<8) + 38 )
6015 | Black olive | BlackOlive | BlackOlive | 41 43 38 | 41 | 43 | 38 | Black olive | #define BlackOlive ((41<<16) + ( 43<<8) + 38 )
6016 | Turquoise green | TurquoiseGreen | TurquoiseGreen | 15 112 51 | 15 | 112 | 51 | Turquoise green | #define TurquoiseGreen ((15<<16) + ( 112<<8) + 51 )
6017 | Yellow green | YellowGreen | YellowGreen | 64 130 54 | 64 | 130 | 54 | Yellow green | #define YellowGreen ((64<<16) + ( 130<<8) + 54 )
6018 | May green | MayGreen | MayGreen | 79 168 51 | 79 | 168 | 51 | May green | #define MayGreen ((79<<16) + ( 168<<8) + 51 )
6019 | Pastel green | PastelGreen | PastelGreen | 191 227 186 | 191 | 227 | 186 | Pastel green | #define PastelGreen ((191<<16) + ( 227<<8) + 186 )
6020 | Chrome green | ChromeGreen | ChromeGreen | 38 56 41 | 38 | 56 | 41 | Chrome green | #define ChromeGreen ((38<<16) + ( 56<<8) + 41 )
6021 | Pale green | PaleGreen | PaleGreen | 133 166 122 | 133 | 166 | 122 | Pale green | #define PaleGreen ((133<<16) + ( 166<<8) + 122 )
6022 | Olive drab | OliveDrab | OliveDrab | 43 38 28 | 43 | 38 | 28 | Olive drab | #define OliveDrab ((43<<16) + ( 38<<8) + 28 )
6024 | Traffic green | TrafficGreen | TrafficGreen | 36 145 64 | 36 | 145 | 64 | Traffic green | #define TrafficGreen ((36<<16) + ( 145<<8) + 64 )
6025 | Fern green | FernGreen | FernGreen | 74 110 51 | 74 | 110 | 51 | Fern green | #define FernGreen ((74<<16) + ( 110<<8) + 51 )
6026 | Opal green | OpalGreen | OpalGreen | 10 92 51 | 10 | 92 | 51 | Opal green | #define OpalGreen ((10<<16) + ( 92<<8) + 51 )
6027 | Light green | LightGreen | LightGreen | 125 204 189 | 125 | 204 | 189 | Light green | #define LightGreen ((125<<16) + ( 204<<8) + 189 )
6028 | Pine green | PineGreen | PineGreen | 38 74 51 | 38 | 74 | 51 | Pine green | #define PineGreen ((38<<16) + ( 74<<8) + 51 )
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

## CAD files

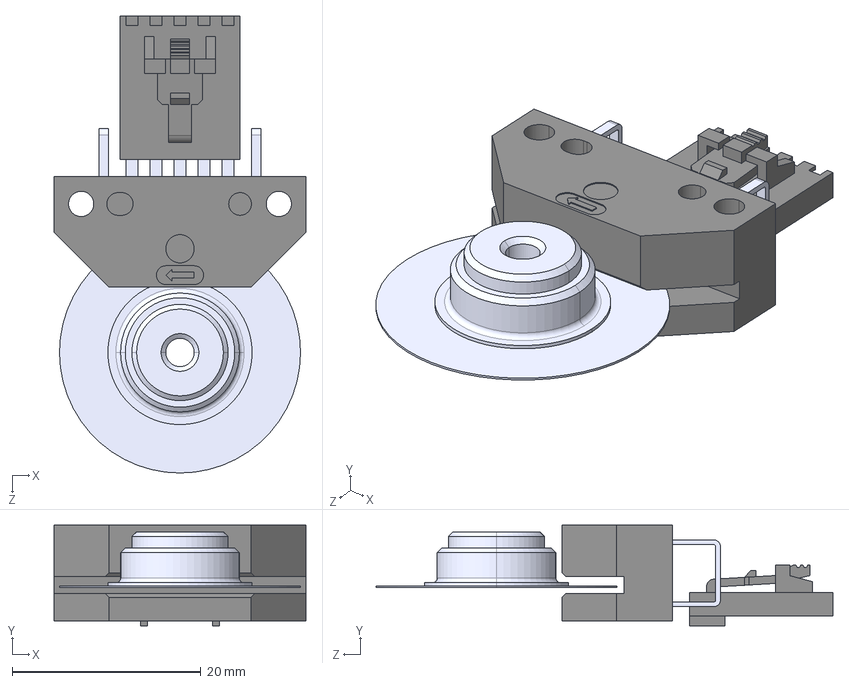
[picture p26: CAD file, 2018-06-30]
CAD/Encoder/ENCODER ASSY.STEP
26.7 x 10.7 x 48.5 mm
HEDS-9040
HEDM-512

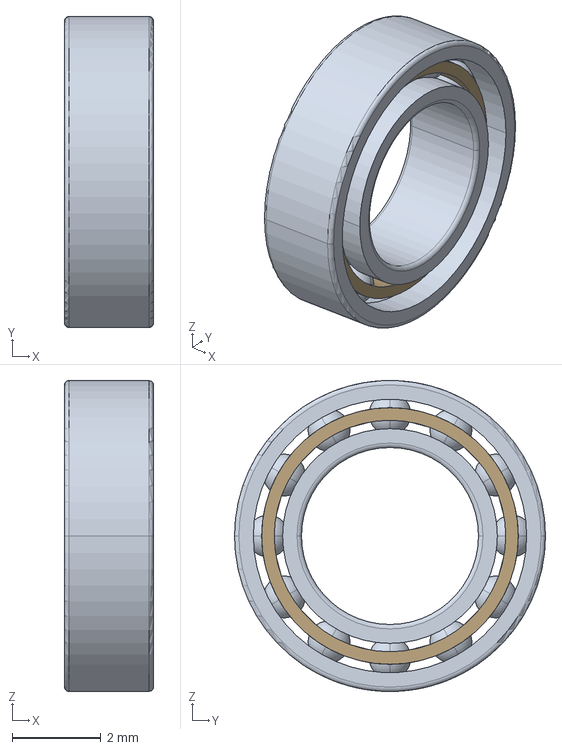
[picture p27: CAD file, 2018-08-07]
CAD/Bearings/AST_Bearings_SMR74.stp
2.01 x 7.01 x 7.01 mm

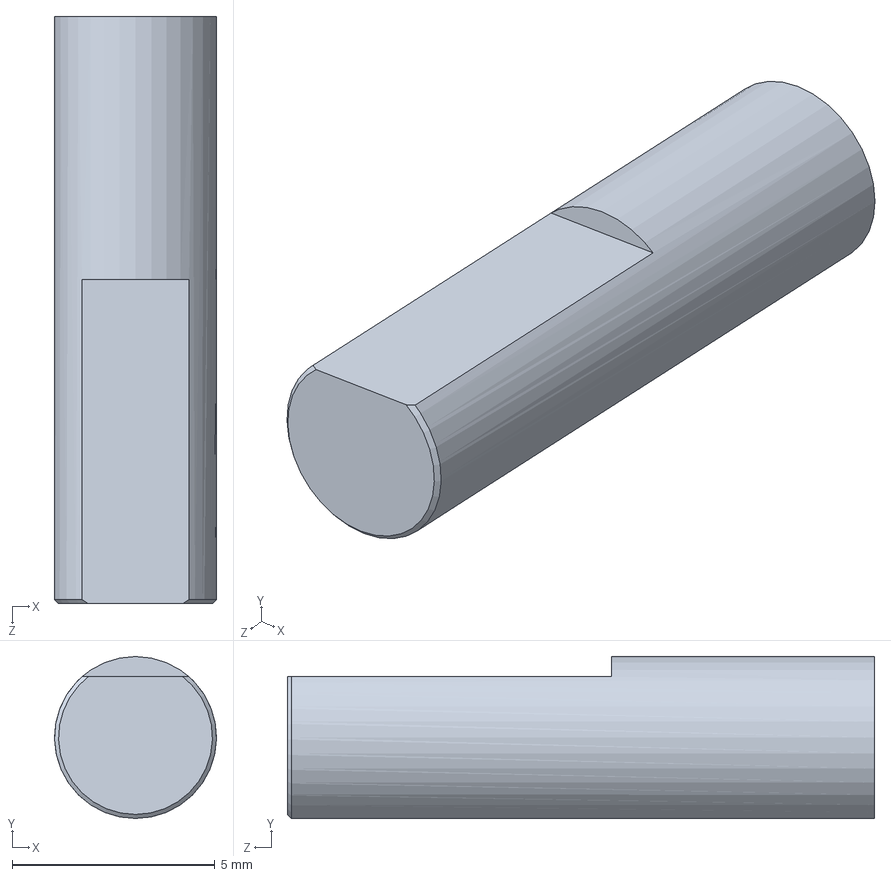
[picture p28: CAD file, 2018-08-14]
CAD/Pololu Motor 25D/Driveshaft.SLDPRT
4.00 x 4.00 x 14.5 mm

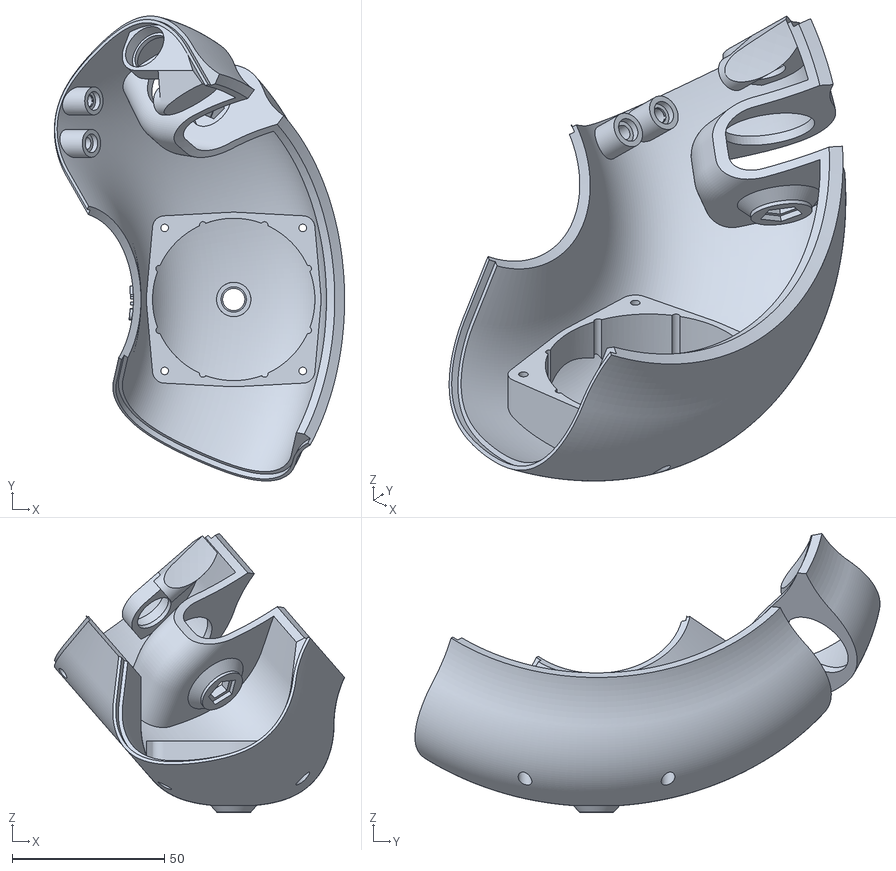
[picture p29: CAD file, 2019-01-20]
stl/Body/Torus.stl
95.5 x 152.9 x 91.8

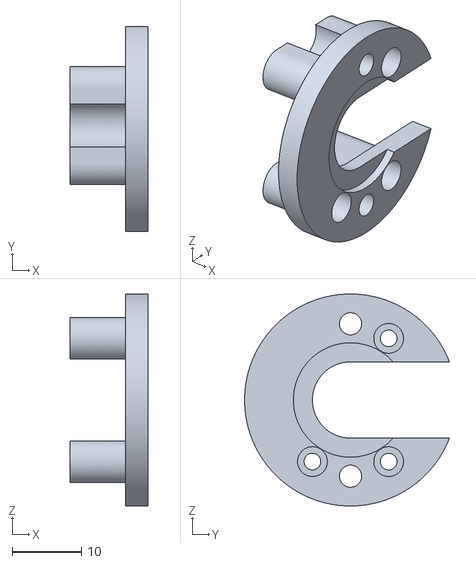
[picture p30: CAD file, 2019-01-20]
stl/Encoder/AS5047DEnclosure.stl
11.2 x 29.6 x 30.6

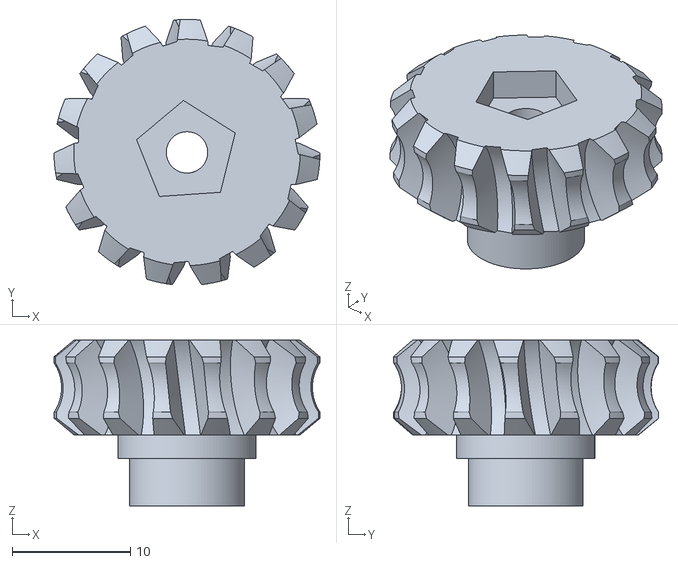
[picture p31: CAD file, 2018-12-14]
stl/Leg/LegGearPinion.stl
22.5 x 22.4 x 14.0

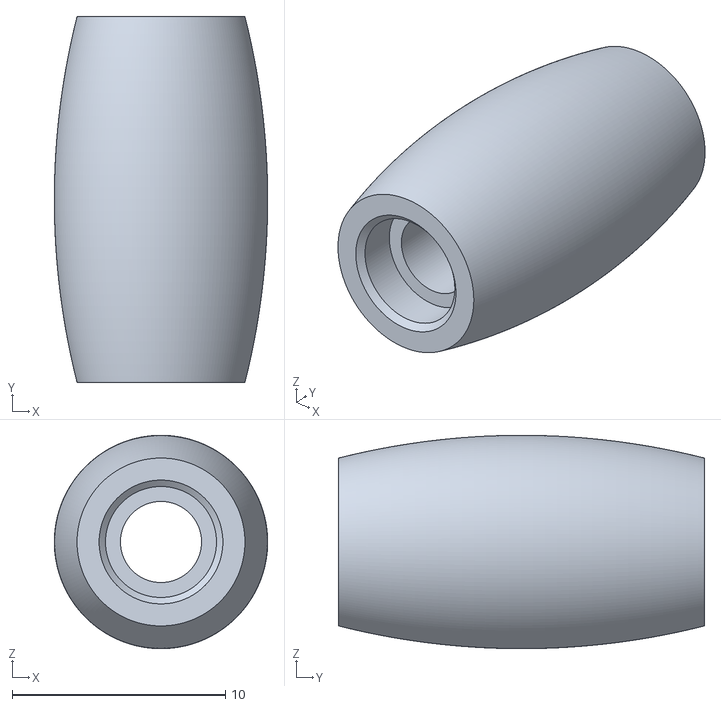
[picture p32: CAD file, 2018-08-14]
stl/OmniWheel/SmallRoll.stl
10.00 x 17.1 x 10.00

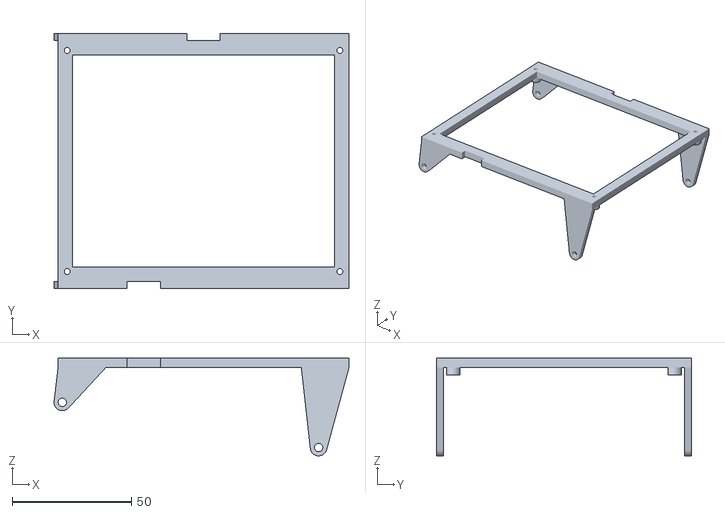
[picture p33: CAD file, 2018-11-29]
stl/PCB/Scaffold.stl
123.7 x 107.0 x 41.0

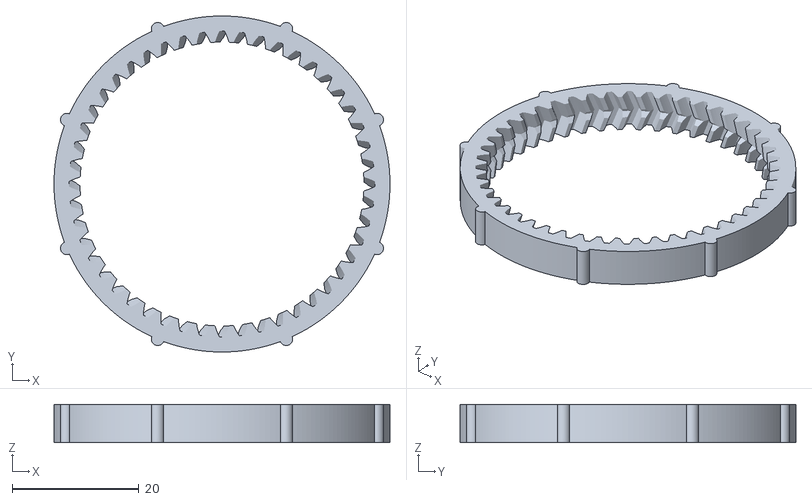
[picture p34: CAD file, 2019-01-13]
stl/PlanetaryGear/OuterWheel.stl
53.0 x 53.0 x 6.00

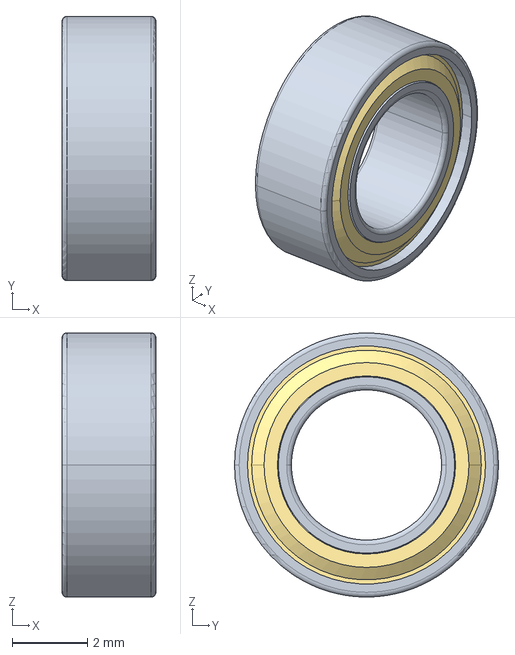
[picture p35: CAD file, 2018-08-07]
CAD/Bearings/AST_Bearings_SMR74ZZ.stp
2.49 x 7.01 x 7.01 mm

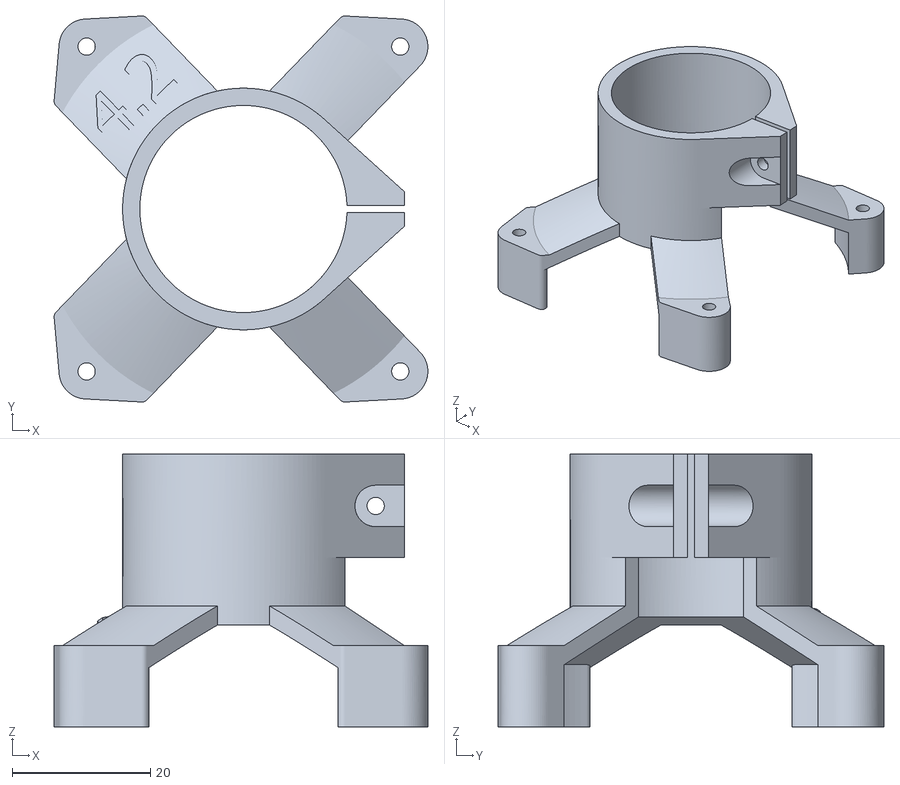
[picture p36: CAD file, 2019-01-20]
stl/Body/MotorHolder.stl
54.1 x 55.9 x 39.5

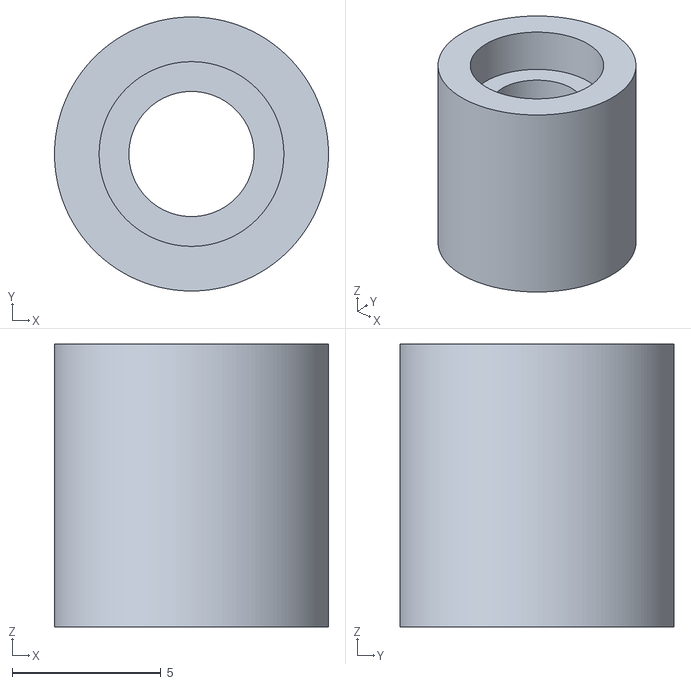
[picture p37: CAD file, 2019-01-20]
stl/Encoder/MagnetHolder.stl
9.20 x 9.20 x 9.50

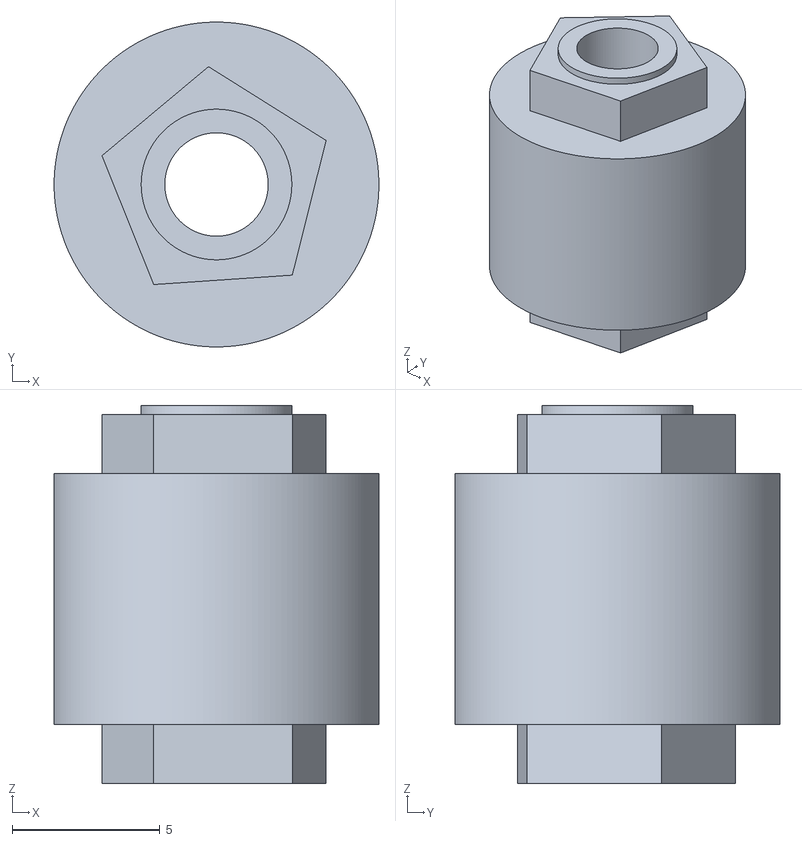
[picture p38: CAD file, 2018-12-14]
stl/Leg/LegGearPinionProlongation.stl
11.0 x 11.0 x 12.8

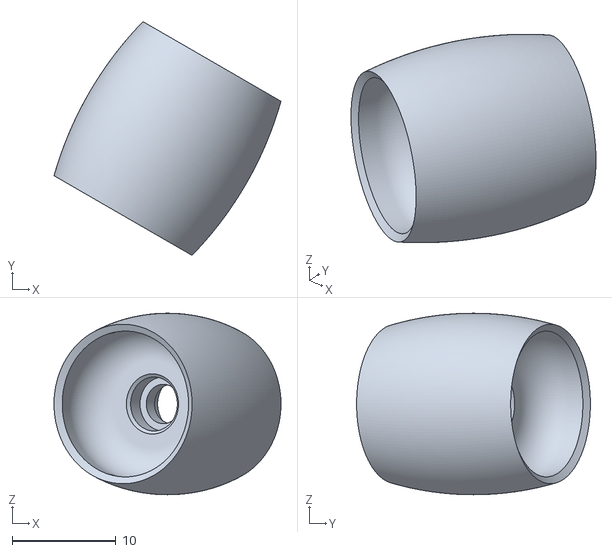
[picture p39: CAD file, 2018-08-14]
stl/OmniWheel/BigRoll.stl
21.9 x 22.5 x 17.5

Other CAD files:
stl/PCB/Holder1.stl
stl/PlanetaryGear/Top.stl
stl/Body/Bottom.stl
stl/Leg/LegBeltMiddle2.stl
CAD/Bearings/AST_Bearings_SMR74.ipt
CAD/Bearings/AST_Bearings_SMR74ZZ.ipt
CAD/Bearings/W 61700 X-2RS1.iam
CAD/Bearings/W 61700 X-2RS1_PART1.ipt
CAD/Bearings/W 61700 X-2RS1_PART2.ipt
CAD/Bearings/W 61700 X-2RS1_PART3.ipt
CAD/Bearings/W 617_3.iam
CAD/Bearings/W 617_3_PART1.ipt
CAD/Bearings/W 617_3_PART2.ipt
CAD/Bearings/W 617_3_PART3.ipt
CAD/Bearings/W 617_3_PART4.ipt
CAD/Bearings/W 618_2 X.iam
CAD/Bearings/W 618_2 X_PART1.ipt
CAD/Bearings/W 618_2 X_PART2.ipt
CAD/Bearings/W 618_2 X_PART3.ipt
CAD/Bearings/W 618_2 X_PART4.ipt
CAD/Bearings/W 627_7-2ZS.iam
CAD/Bearings/W 627_7-2ZS_PART1.ipt
CAD/Bearings/W 627_7-2ZS_PART2.ipt
CAD/Bearings/W 627_7-2ZS_PART3.ipt
CAD/Bearings/W 627_7-2ZS_PART4.ipt
CAD/Bearings/W 637_4 X-2Z.iam
CAD/Bearings/W 637_4 X-2Z_PART1.ipt
CAD/Bearings/W 637_4 X-2Z_PART2.ipt
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

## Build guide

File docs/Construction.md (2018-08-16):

Inverse kinematics, i.e. computation of joint angles out of the gripper’s position can be hard. If the design is too playful, nearly impossible complex. So, it is a good idea to ease the maths by having the upper three axes intersecting in one point. Later in the chapter on kinematics we will see that with that limitation kinematics becomes possible without having a mathematician at hand (still not easy, but feasible). 

## Dimensioning 

Before starting the design it is necessary to calculate the torque in all actuators in order to select the steppers and gear ratios properly. In principle, this is simple: The gripper should be able to manipulate 500gr, the forarm has a length of 400mm and the upper arm a length of 350mm, assuming a certain weight per actuator the law of the lever allows to compute the torque of each motor. Tricky part is, that depending on the stepper you choose, the weight of an actuator changes.  In the end I did that computation with excel, and came to these torques 
and gear ratios, which are used to select the stepper's dimensions.

| Actuator | Computed Torque | Gear  | Min Stepper Torque | Selected Stepper Size  | Act. Stepper Torque | 
|--- |---|--- | --- | --- | --- |
| Wrist | 0.6 Nm |  1:4  | 0.18 Nm | NEMA 17 42x42x39 | 0.4 Nm |
| Elbow | 0.6 Nm |  1:7  | 0.11 Nm | NEMA 17 42x42x25 | 0.17 Nm |
| Forearm  | 11 Nm |  1:14 | 0.8 Nm | NEMA 24 60x60x57 | 1.9 Nm |
| Upper arm| 34 Nm |  1:18 | 1.8 Nm | NEMA 24 60x60x87 | 3 Nm |
| Hip | 8 Nm |  1:9  | 0.9 Nm | NEMA 23 57x57x56 | 1.2 Nm |

The steppers are always placed in the previous joint of an actuator in order to move the centre of gravity away from the biggest lever. So, the three heavy steppers actually do not move but turn only when the arm goes up or down.

## Design Patterns

With that amount of torque, shaft-hub joints need to be really stable. While the small steppers have the pulley connected with grub screws, the big ones need something different. Although a lot of filing was involved, I went with feather keys for the middle shaft of gearboxes and the connection between stepper motor and timing pulley.




## Gripper

Due to space limitations, it seems to be appropriate to use a servo for the gripper. I used a standard design principle where one lever is driven, and the other lever mirrors the movement by a gear wheel. The servo is hidden in a small box, it is a HerkuleX Robot Servo with 0.12 Nm (today I would take the stronger version of the same servo, 0.12Nm is just enough to lift a beer).







Assembly has to start from the top, not for mechanical reasons, but due to the cables that are all placed inside the robot going down from the gripper to the base.
The gripper has bearings in all moving parts. The left gearwheel has the servo behind, mounted on the enclosed servo disk. To increase stability, the hole over the servo screw is used for another bearing to lock this lever from both sides in its position.


The servo's cable is going through the servo housing into the flange where the wrist will be placed.

I'm still not really happy with the gripper. Although it works fine, the bulge containing the servo is really ugly. But, the space below the gripper is already occupied by the servo turning the wrist, unfortunately. I played with other design types, but always came back to this one due to its simplicity.

## Wrist

The wrist is also designed with the same servo. A small flange connects the wrist with the two halves of the gripper housing, the hole hides the cable of the gripper servo. Worth to mention is that bearings at both sides of the wrist have a different size, since the servo looks through the inner hole of the bigger bearing. On the other side, in the middle of the smaller bearing there is the hole for the magnet used by the magnetic encoder of the forearm. The cable of both servos (gripper and wrist) is going through the wrist underneath the servo.



The gripper is held with only one extra loose bearing,  since the servo provides the fixed bearing already. The servo is mounted on the back of the wrist with screws. The servohorn is mounted to the flange that links the wrist to the gripper.

The bearing at the right side, that is marked with a red circle is very close to the inner diameter of the belt pulley. This space is occupied by the forearm to fix the bearing with a thin ring. The ring can be seen on the following CAD drawing, also marked with a red circle.

## Forearm

The forearm is more complex, since it drives the wrist with a belt drive and a stepper motor. The belt drive has a gear ratio of 1:4. It is held tight with a spanner. At the other side of the wrist, the magnetic encoder is located. All cables are meeting in the room below the stepper at the bottom, and going down through the hole of the disk.



Below, the magnet in the middle of the wrist's bearing can be seen, which has a distance of 1mm to the magnetic encoder of the other half of the forearm.



## Elbow

The elbow consumed most design-time, it is a two stage belt-drive with a ratio of 1:7 and a stepper with 17Ncm. The flange in the middle is the connection to the forearm. It is mounted with two  bigger bearings and has a cable channel that gives space to a self made cable drag chain that allows to have the cables inside, since the centre of the axis is occupied by the encoder already.



This picture shows the inner construction and the cable drag chain. The magnet in the centre of the flange is right opposite to the encoder, the small PCB in the middle of the ellbow.


At first, I tried to hide the belt pulley within the enclosure, but later on I got the impression that a peep hole exposing a pulley moving faster than the elbow could be a nice technical touch.



## Upper Arm

The upper arm contains a strong stepper with 1.9Nm and a two-staged gear with a ratio of 1:14. On the left side a magnetic encoder samples the angle of the ellbow, above the encoder and the cable channel is located. The cables are going down through a hole in the middle block down to the left side of the bttom part. The ride side contains the belt to the elbow. All belts are tighened with a clamp that can be adjusted from outside.



The cable is going through the centre of the axis. Below the fork of the upper arm, the gearbox is placed.



Right above the belt pinion of the stepper, the magnet for the encoder is placed, in the middle of the space intended for the cables. The thin space between the bearing and the housing will be required by the shoulder actuator to hold the upper arm.


## Shoulder

The shoulder contains the strongest stepper moving the upper arm with approx. 3 Nm. A gear ratio of 1:18 could deliver 50Nm, but this number is rather theoretical, since 3D-printed parts would not survive this. But, this allows to reduce the current and use micro-stepping improving the movement.

On the left flange, there is a segment-shaped cable channel below the location of the magnetic encoder. The right flange has a big hole to make room for the stepper's backside. This is hidden by a lid that rotates with the upper arm, which gives a nice technical touch. Inside the middle block between the flanges, there is a shaft with two drive pulleys for the two-staged gearbox, same construction as in the upper arm.




## Hip

Finally, the hip stepper is what makes the housing of the shoulder look like an iglu. It is a simple belt drive to the shoulder. The shoulder is residing on a drive pulley disk that is mounted on a big bearing.



The encoder is mounted within the inner base, the magnet is mounted at the outer belt wheel, in between is a big bearing.





## Housing

The housing of the shoulder is not only to hide the hip stepper, but also to stabilize the shoulder by having lots of small bearings on the top edge supporting the shoulder. The inner compartments of the flower pot is filled with iron grain, which has a mass of approx 5kg



The middle layer of the pot is not printed but made of wood for stability reasons. Besides that, I like the look of birch plywood:




## Cable

Last but not least, a beautiful cable sleeve accompagnies Walter's color. Since all electronics is in the control cabinet, the cable has 5x4 pins for the steppers, 4 pins for the servo's serial connection and 2x 4 pins for the two I2C busses.



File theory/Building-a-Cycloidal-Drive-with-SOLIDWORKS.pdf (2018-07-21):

# Building a Cycloidal Drive with SOLIDWORKS

By Omar Younis

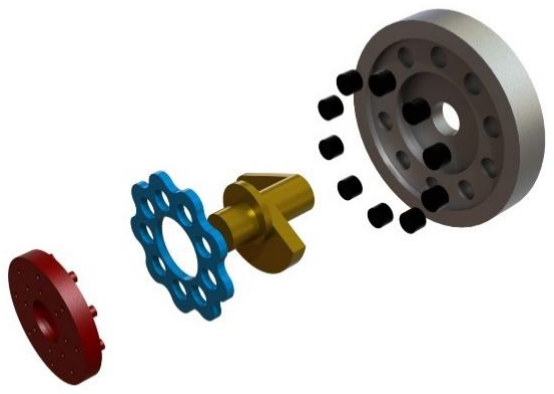
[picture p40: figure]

A Cycloidal Drive is a mechanism used in the engineering world as a speed reducer for an input shaft while reversing its direction. It is able to do this for high ratios in a small space. They do this using a rotor that has a unique motion (see Cycloidal Drive Motion Animation.avi).

In this tutorial I will be going over how to make a Cycloidal Drive in SolidWorks. Some of the features that we will be using are the Parametric Feature on the Equation Driven Curve tool and the CAM Mate used in assemblies.

There are five main parts to a Cycloidal Drive: the Rotor, the Output Disk (could equally be an output shaft), the Input Shaft, the Rollers and the Main Housing (See Figure 3). Let’s start by making the more complex part of the Cycloidal Drive, the Rotor.

Figure 1 | Figure 2

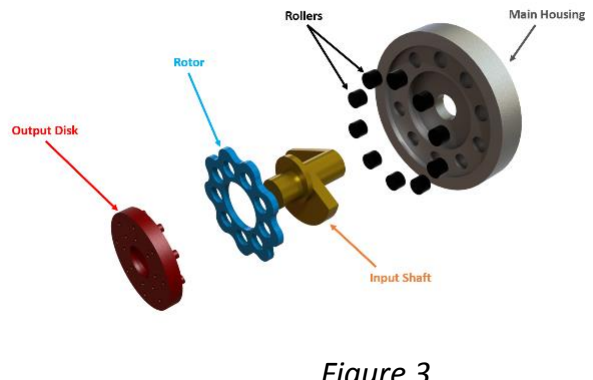
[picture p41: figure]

Figure 3

### Rotor

As you can see, the Rotor has a very unique shape (See Figure 4); something that wouldn’t be easily constructed using the basic sketch tools that SolidWorks gives you. So what do we do? Luckily SolidWorks comes to our rescue with a tool that will make making this part a breeze, the Equation Driven Curve tool! There are two different types of equations that can be used, Explicit equations and Parametric equations. The Explicit Equations are used when you have a single variable equation such as y = x

2
. The way Explicit works is that it creates a
curve of an equation that you give it from two

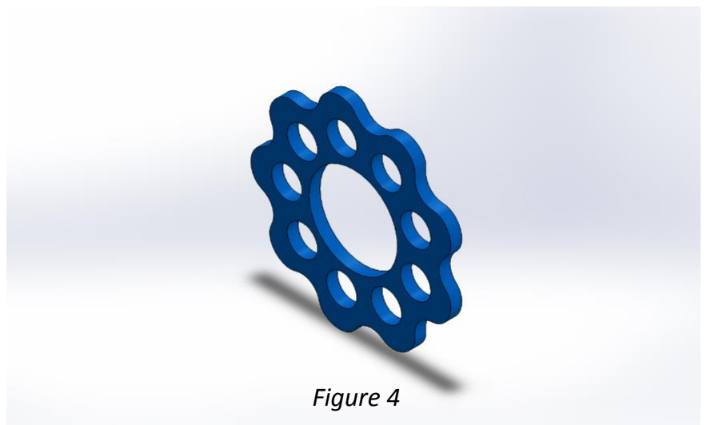
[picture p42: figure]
Figure 4

different points. For example you can make a line based on the curve y = x² starting from 0 and ending at
10. Using Parametric Curves works the same way as the Explicit but the only difference is that you use two equations to define a curve (an x-component and a y-component). For our purposes we are going to need to use a Parametric Curve because of the two equations needed to define the Rotor.

The two equations that define the Rotor’s shape are the following:

( ) | ( | ) | ( | )
( ) | ( | ) | ( | )
| Where
[
(( | ) )
( ⁄ | ) | (( | ) )
] | (
)

For the equation we have a say in four parameters. “R” is the radius of the Rotor that you want, “E” is the eccentricity (or offset) from the Input Shaft to the center of the Rotor, “Rr” is the radius of the Rollers and finally “N” which is the number of Rollers. So to save you guys some time and effort I have taken the equations above and put them in a format that SolidWorks can understand so that you can just copy it into SolidWorks. All you have to do is select the parameters you want.

X = (R*cos(t))-(Rr*cos(t+arctan(sin((1-N)*t)/((R/EN)-cos((1-N)*t)))))-(E*cos(N*t))

Y = (-R*sin(t))+(Rr*sin(t+arctan(sin((1-N)*t)/((R/EN)-cos((1-N)*t)))))+(E*sin(N*t))

So now that we have the equations we can start to build our Rotor. For this tutorial I will be using the following parameters for my Rotor: R = 10, E = 0.75, Rr = 1.5, N = 10. I will also be using the ANSI standard with IPS units.

In a new part file create a sketch on the front plane. Next select the Equation Driven Curve tool from the Sketch Entities tools.

Once in the Equation Driven Curve Wizard, select the parametric option.

Once you have selected the Parametric option, the wizard should change. Now you should have a place to input two equations, one for the x-component and one for the y-component. Input the Rotor’s equations for the x and y components in the correct boxes.

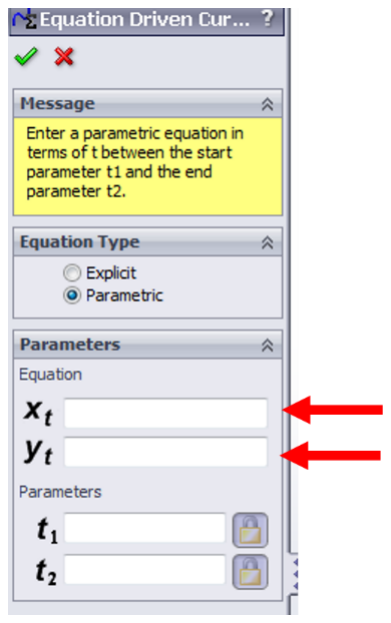
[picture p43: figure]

The next two boxes labeled t1 and t2 are where you put your start and end conditions for the curve.

Since we want to have a complete Rotor it would be logical to assume that our t1 and t2 would be 0° and 360° respectively (or 0 to 2π). Unfortunately SolidWorks doesn’t like curves that start and end at the same point in space. So what’s the solution? Well, we could make two curves: one that goes from 0 to 180° and then another from 180° to 360°. In fact that is what I tried after I discovered at going from 0° to 360° wasn’t a viable option. Unfortunately, even though this gets you the desired shape you want, it comes with a price. What happens is that at the two points were the curves meet an infinitesimally small peek and valley is created making it almost impossible for some assembly mates to work properly; such as a CAM mate.

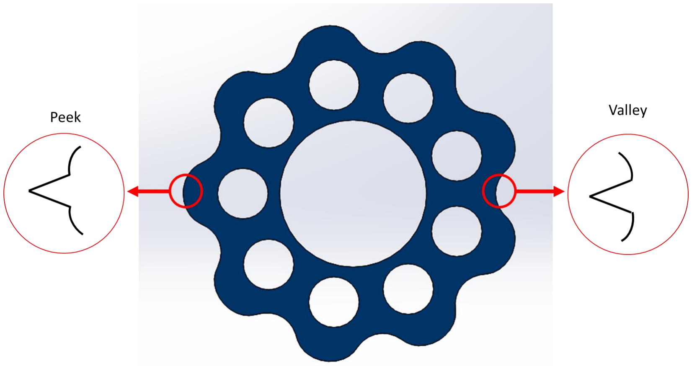
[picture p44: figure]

So now what? Well there is a solution to this problem, but it isn’t as straight forward as you would think and what helps us is that the Rotor has at least one line of symmetry. Since we want to have tangency around the entire shape, what we need to do is we need to create two halves of the overall shape but not by going from 0° to 180° and then from 180° to 360°. What we actually need to do it create one half of the shape by going from -10° to 190°, create a line of symmetry and remove the extra parts of the line. We then need to take our curve and mirror it about the line of symmetry and finally add a tangent relationship between the two curves.

In the Equation Driven Curve wizard under the parametric option after you have entered in your two equations (one for the x-component and one for the y-component) enter -10°
for t1 and 190° for t2. They should both be entered in radians not degrees. You can uses the following equation so that all you need to do is enter the desired degree angle you want were the variable “x” is: (x/360)*(2*pi). Also you can use the following equations for the rotor profile if you are using the numbers I provided earlier:

X = (10*cos(t))-(1.5*cos(t+arctan(sin(-9*t)/((4/3)-cos(-9*t)))))-(0.75*cos(10*t))

Y = (-10*sin(t))+(1.5*sin(t+arctan(sin(-9*t)/((4/3)-cos(-9*t)))))+(0.75*sin(10*t))

Once you have done that you should see a preview of the curve that will be generated. If you don’t see the preview click the “Graphics Window” and “Zoom Fit” (which you can do by pressing “F” on your keyboard) to see it. Click the green check mark to generate the curve.

Next draw a centerline that goes through the curve as well as through the Origin and trim the extra parts of the curve with the “Power Trim Tool”.

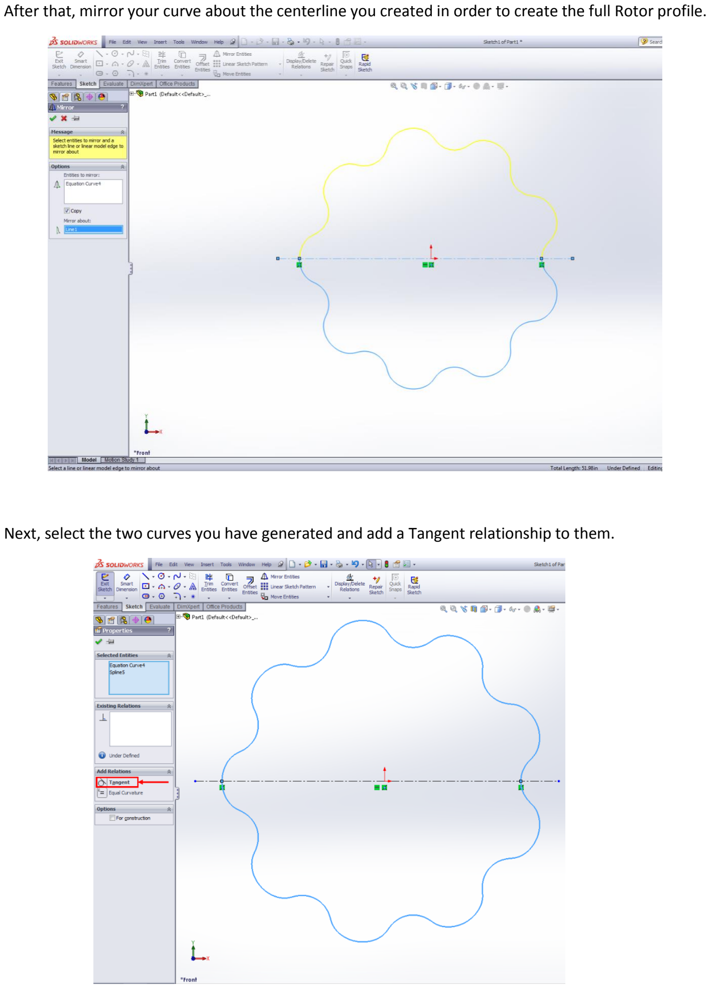
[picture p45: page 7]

After that, mirror your curve about the centerline you created in order to create the full Rotor profile.

Next, select the two curves you have generated and add a Tangent relationship to them.

Congratulations, you have no successfully created the profile of the Rotor for a Cycloidal Drive! Next step is to extrude (Blind Extrude) so we can get a part. If you are following my dimensions then extrude the sketch to 1 inch. Next we need to add a few holes to the Rotor; the hole that will allow the Input Shaft to spin and the holes needed to spin the Output Disk. The only critical dimension is thatthe hole for the Input Shaft is in the middle of the Rotor and that the holes for the Output Disk are in line with each lobe of the Rotor.

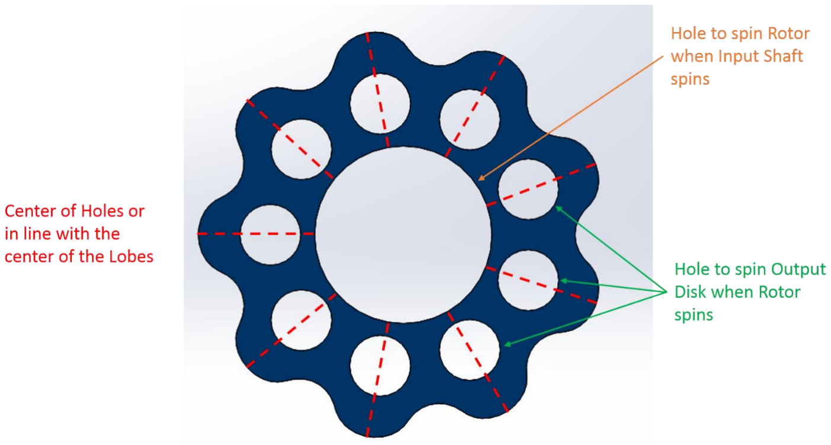
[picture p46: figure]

Another thing is that the diameter for the hole that spin the Output Disk equal to the size of the pins that the Output Disk has added to your eccentricity value. In my case I wanted the pins of the Output Disk to be 2 inches in diameter which meant that the holes needed to be 2.75 inches in diameter since the eccentricity value that I am using is 0.75 inches. So for those who are using my dimensions, below is a quick drawing telling you the dimensions of the holes and there they are located.

To get the holes in the right position, create Hole 1 as shown below and then linear pattern the other holes. This will line up the holes perfectly with the lobes.

Once you are done with the holes, you are now done with the Rotor.

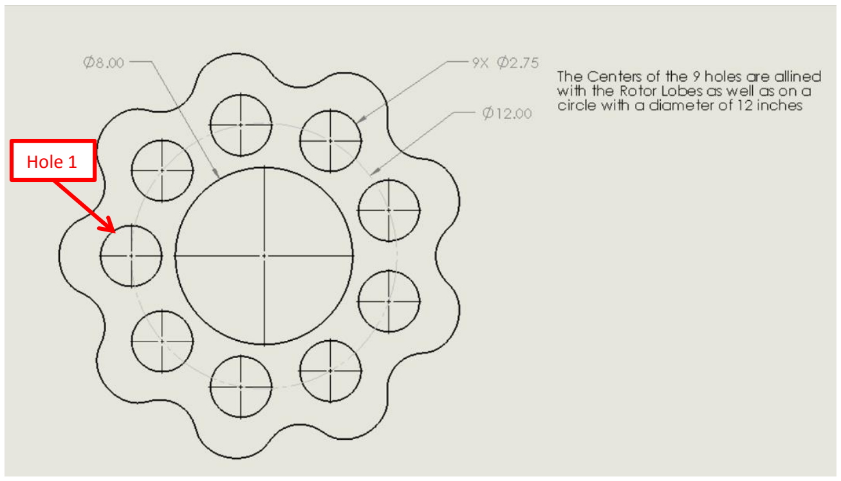
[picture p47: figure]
Hole 1

### Rotor Housing

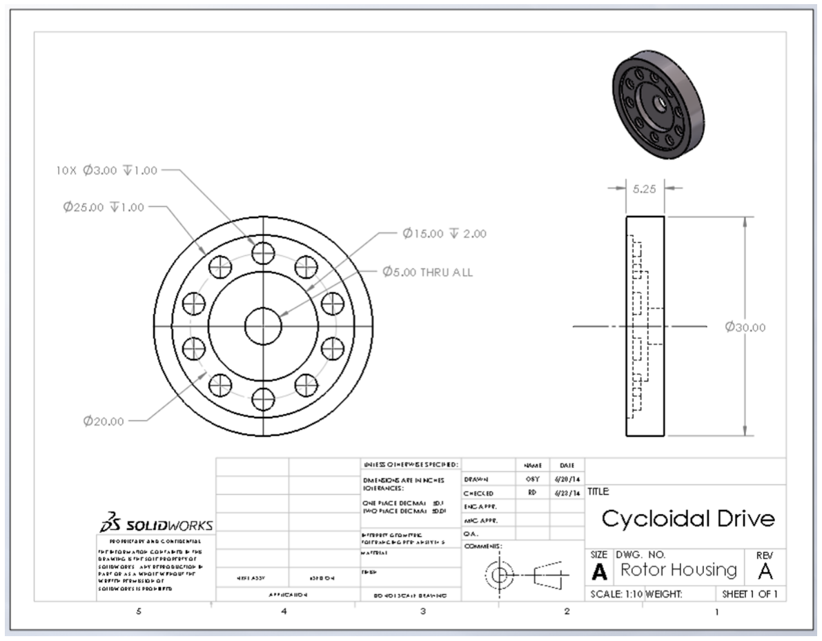
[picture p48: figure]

### Rotor Shaft

### Roller

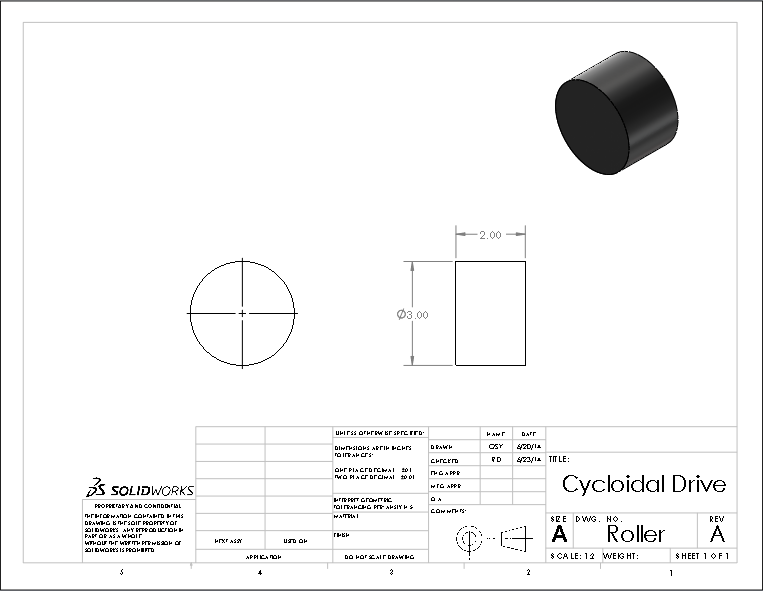
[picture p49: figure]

### Output Disk

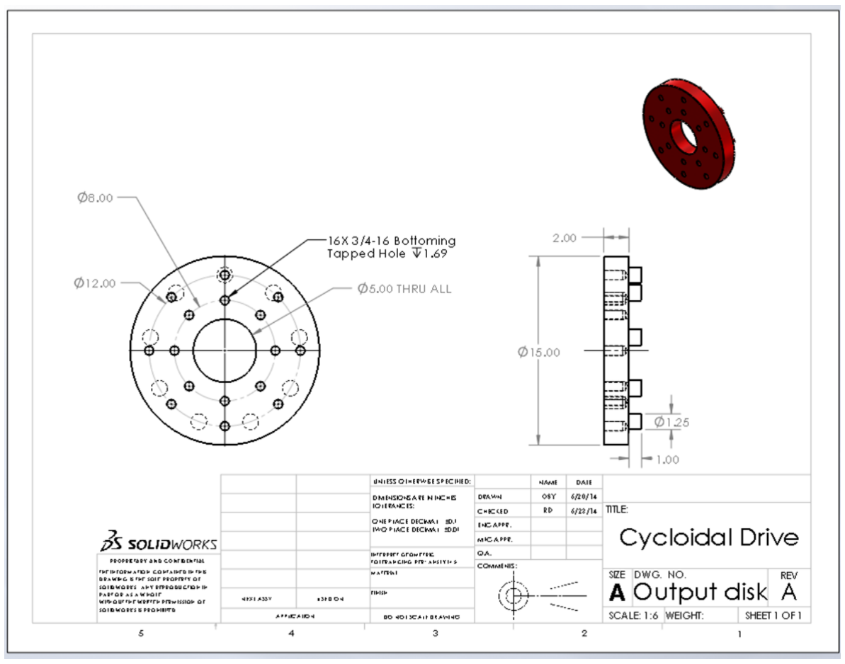
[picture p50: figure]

### Assembling the Drive

Now that we have all the parts build we need, we can start assembling the drive. The drive consists of one sub-assembly which we will be doing first.

First, start of by opening a new assembly file in SolidWorks. Once the file opens the insert component wizard should automatically be selected.

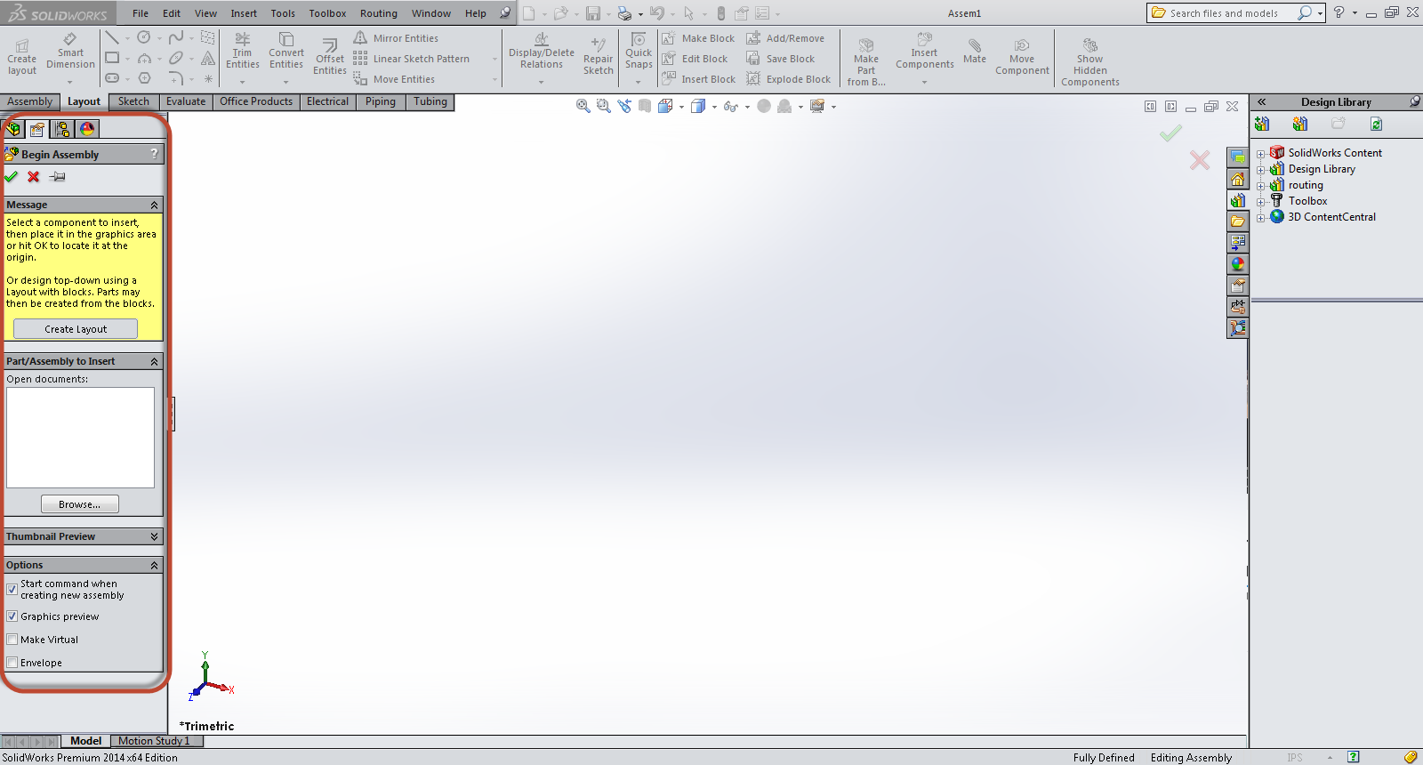
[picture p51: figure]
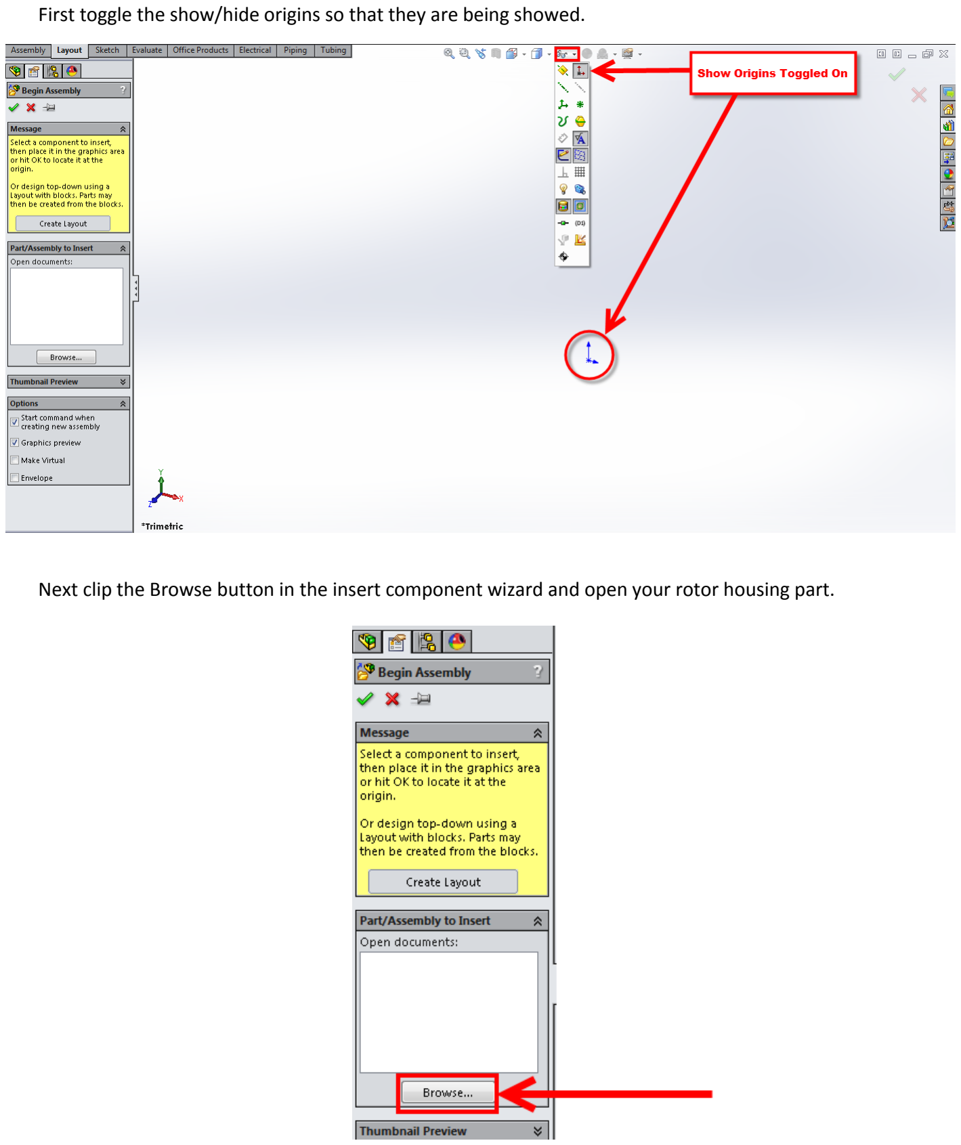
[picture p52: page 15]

First toggle the show/hide origins so that they are being showed.

Next clip the Browse button in the insert component wizard and open your rotor housing part.

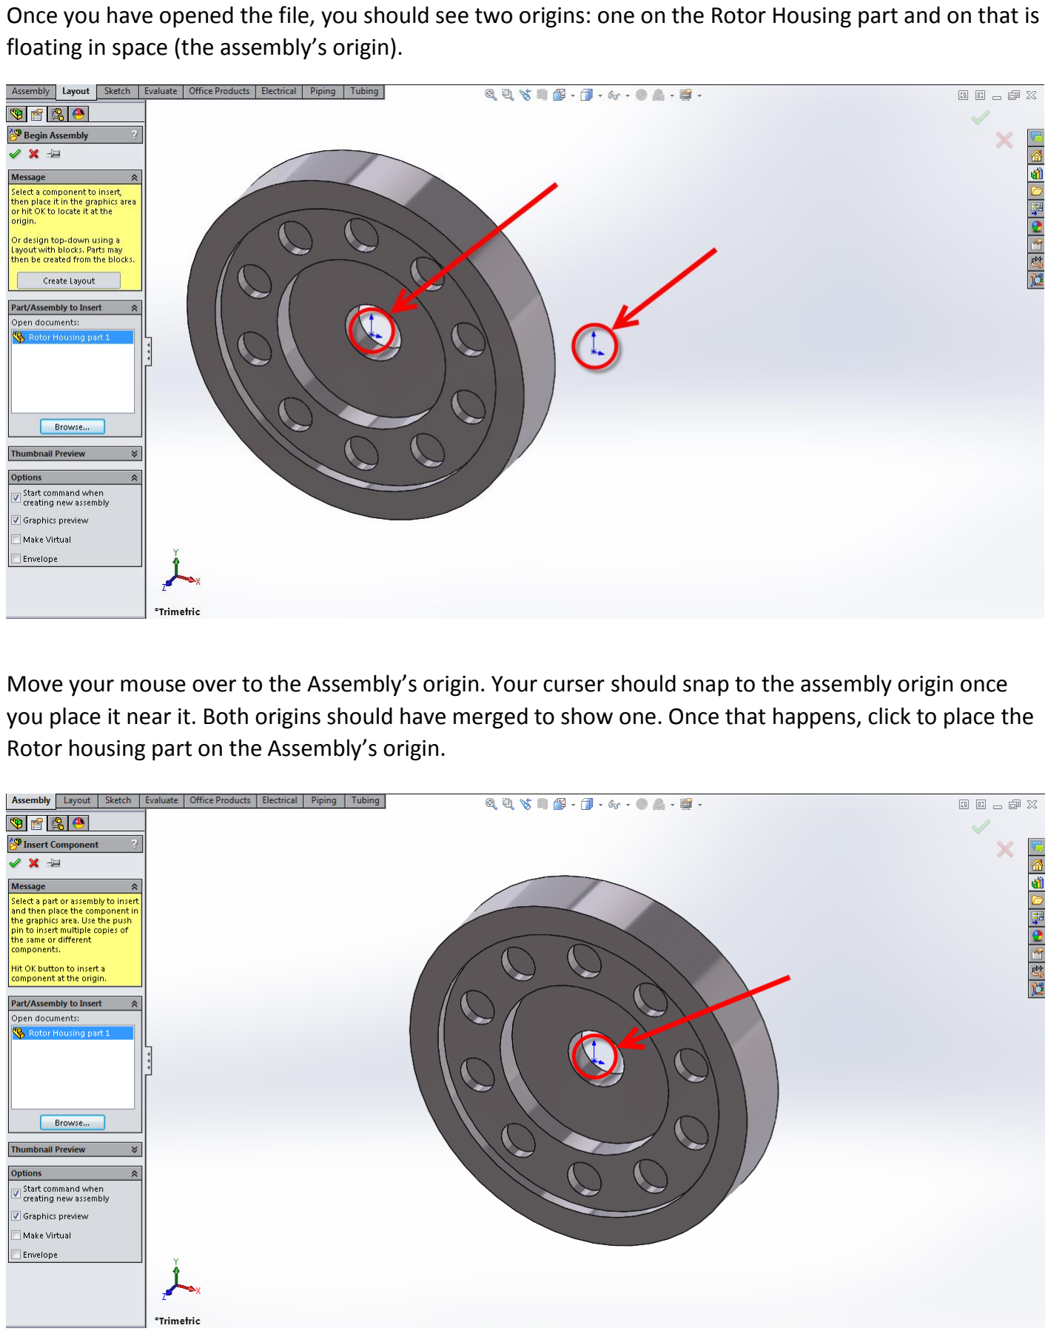
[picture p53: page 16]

Once you have opened the file, you should see two origins: one on the Rotor Housing part and on that is floating in space (the assembly’s origin).

Move your mouse over to the Assembly’s origin. Your curser should snap to the assembly origin once you place it near it. Both origins should have merged to show one. Once that happens, click to place the Rotor housing part on the Assembly’s origin.

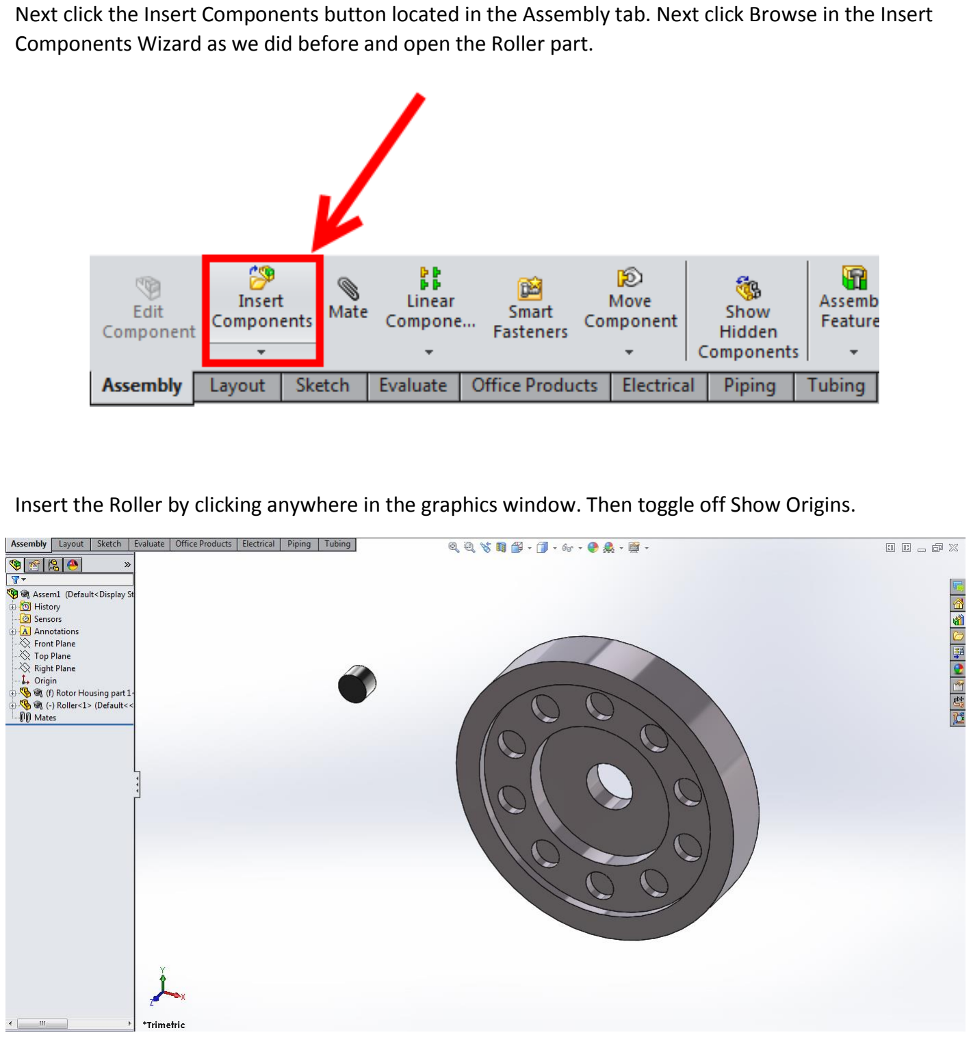
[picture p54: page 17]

Next click the Insert Components button located in the Assembly tab. Next click Browse in the Insert Components Wizard as we did before and open the Roller part.

Insert the Roller by clicking anywhere in the graphics window. Then toggle off Show Origins.

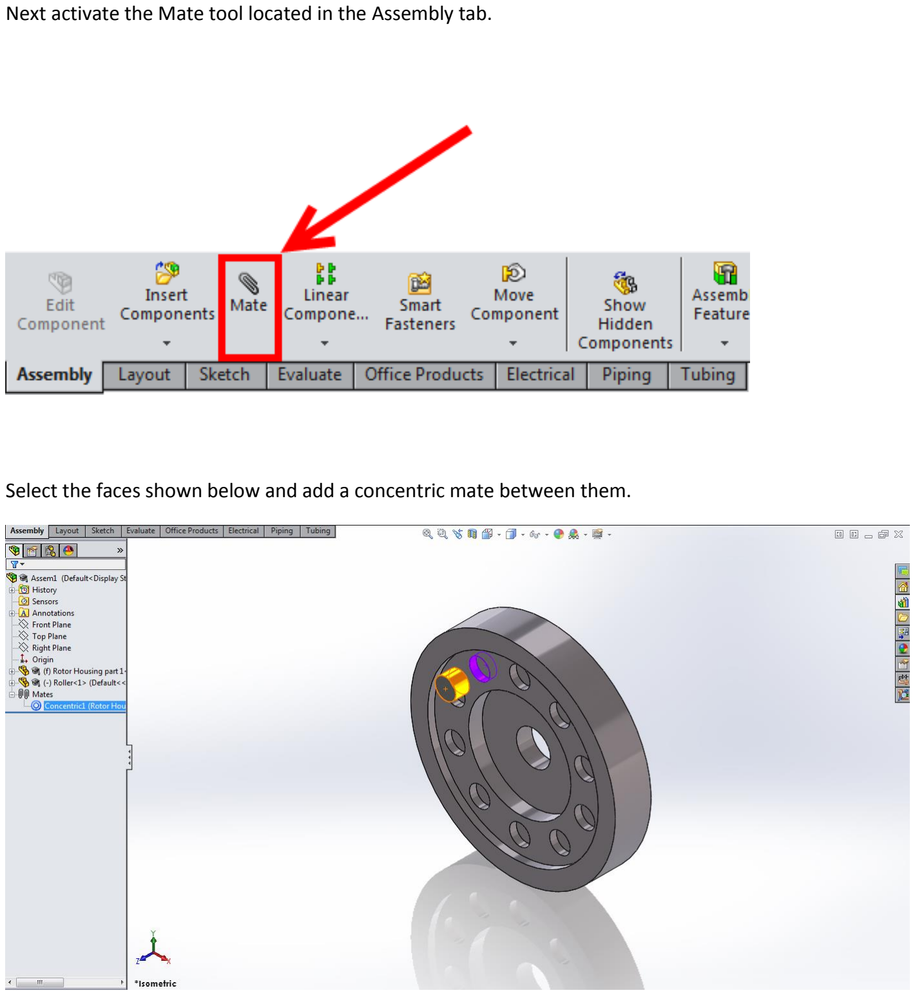
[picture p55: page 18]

Next activate the Mate tool located in the Assembly tab.

Select the faces shown below and add a concentric mate between them.

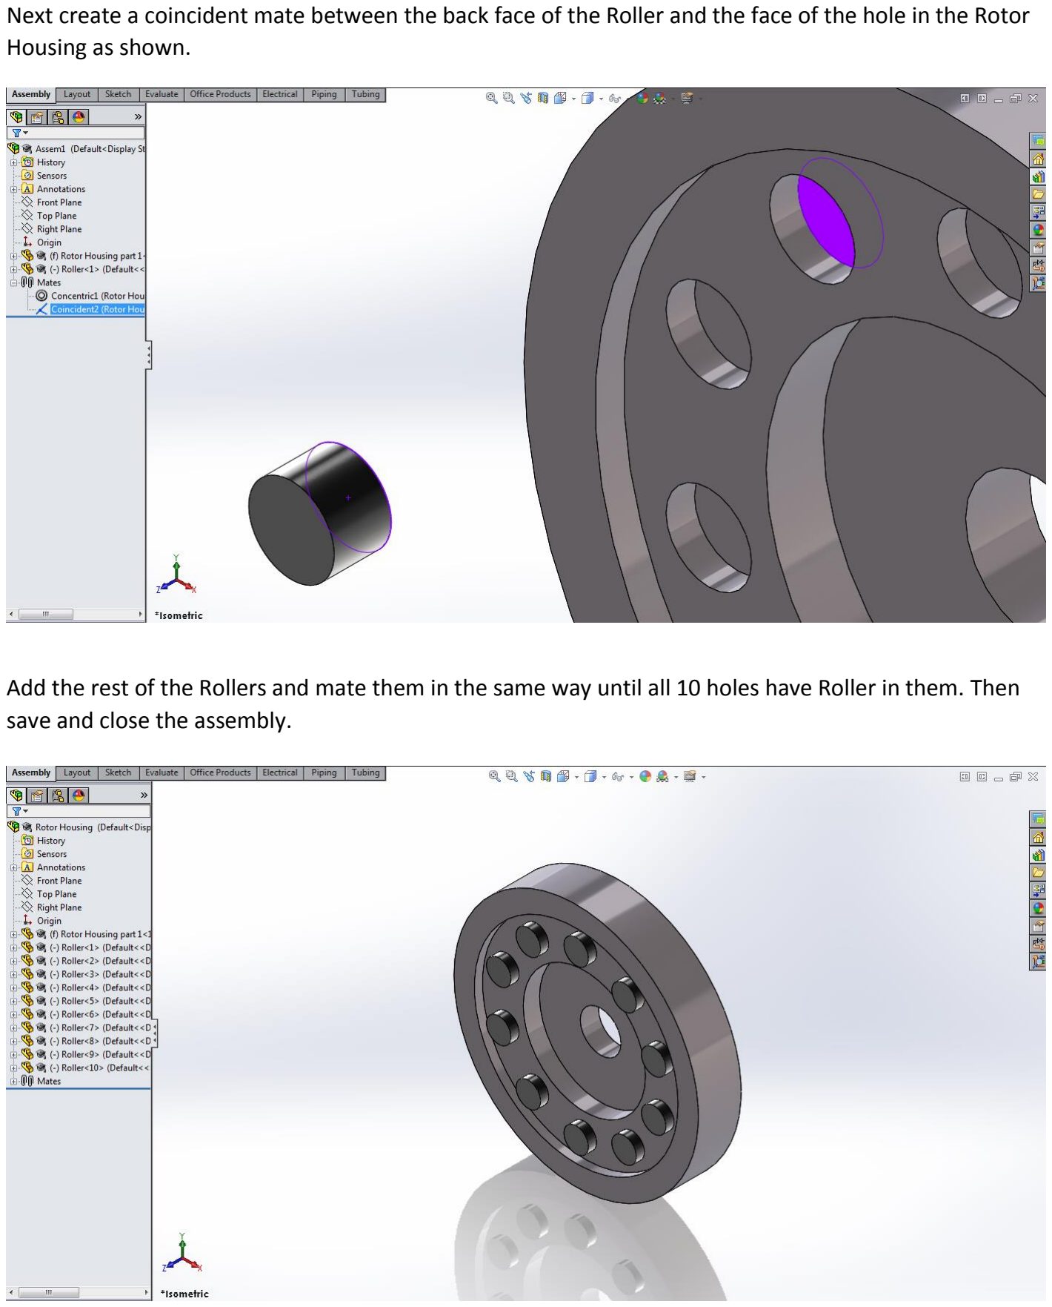
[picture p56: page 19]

Next create a coincident mate between the back face of the Roller and the face of the hole in the Rotor Housing as shown.

Add the rest of the Rollers and mate them in the same way until all 10 holes have Roller in them. Then save and close the assembly.

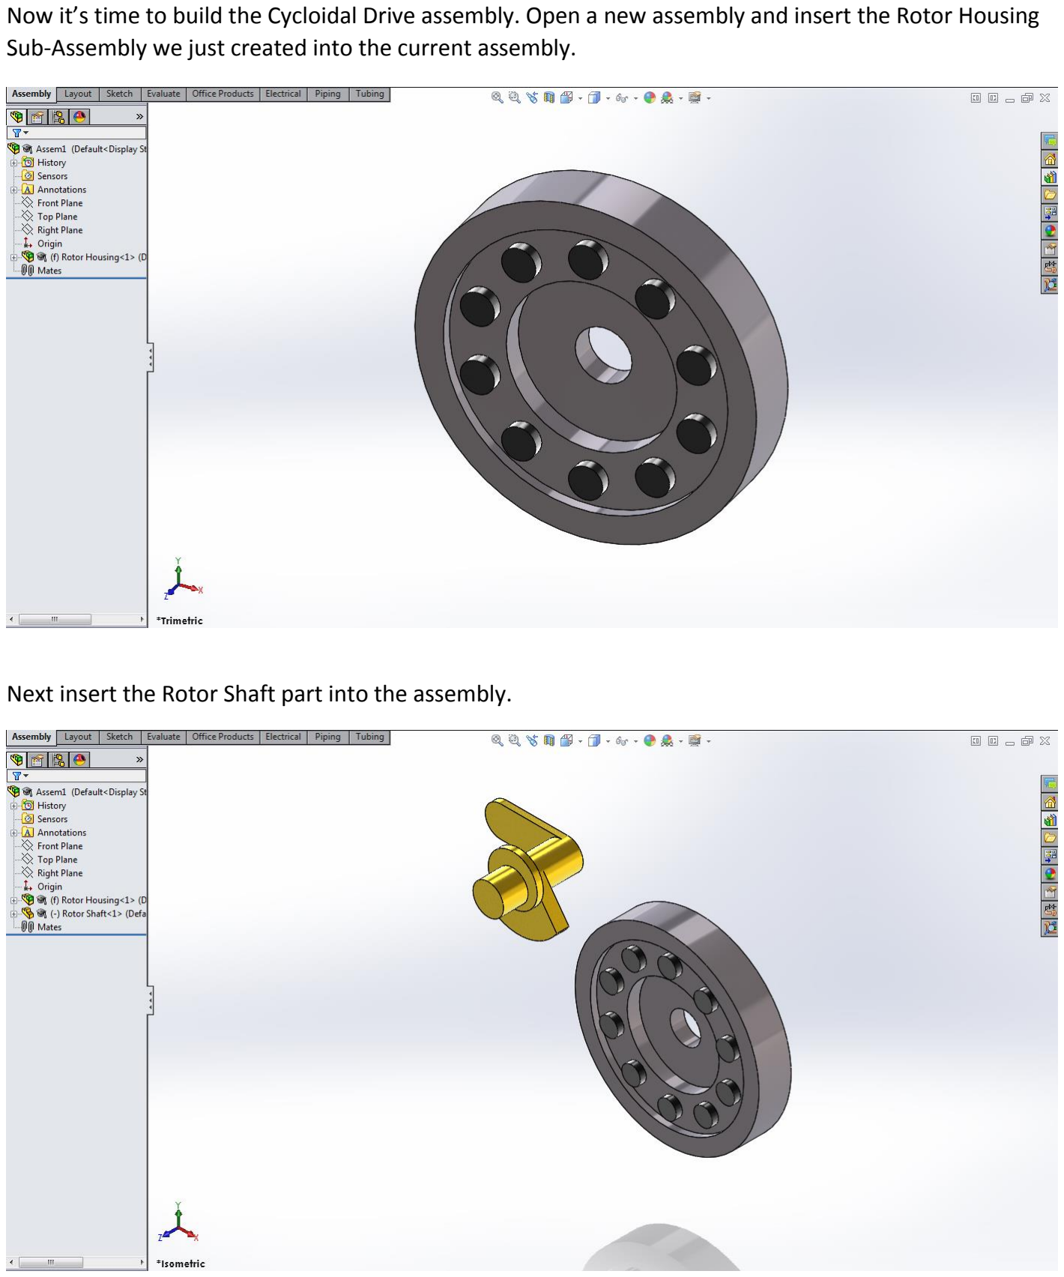
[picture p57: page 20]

Now it’s time to build the Cycloidal Drive assembly. Open a new assembly and insert the Rotor Housing Sub-Assembly we just created into the current assembly.

Next insert the Rotor Shaft part into the assembly.

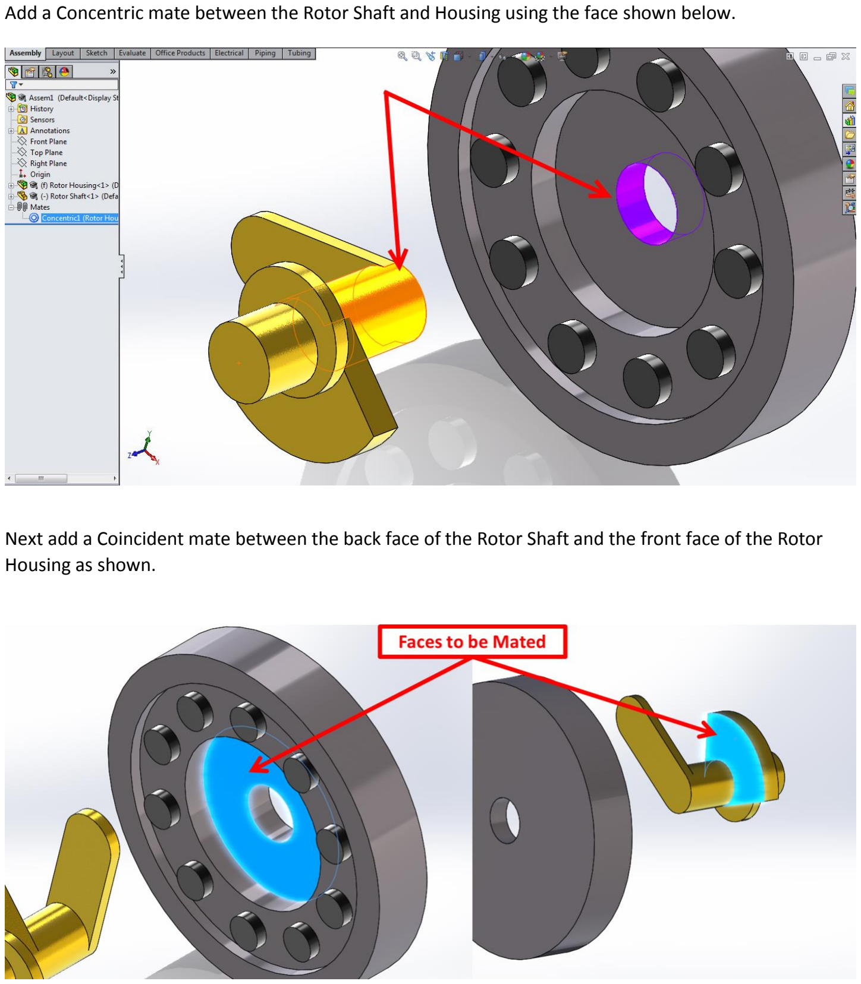
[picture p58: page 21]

Add a Concentric mate between the Rotor Shaft and Housing using the face shown below.

Next add a Coincident mate between the back face of the Rotor Shaft and the front face of the Rotor Housing as shown.

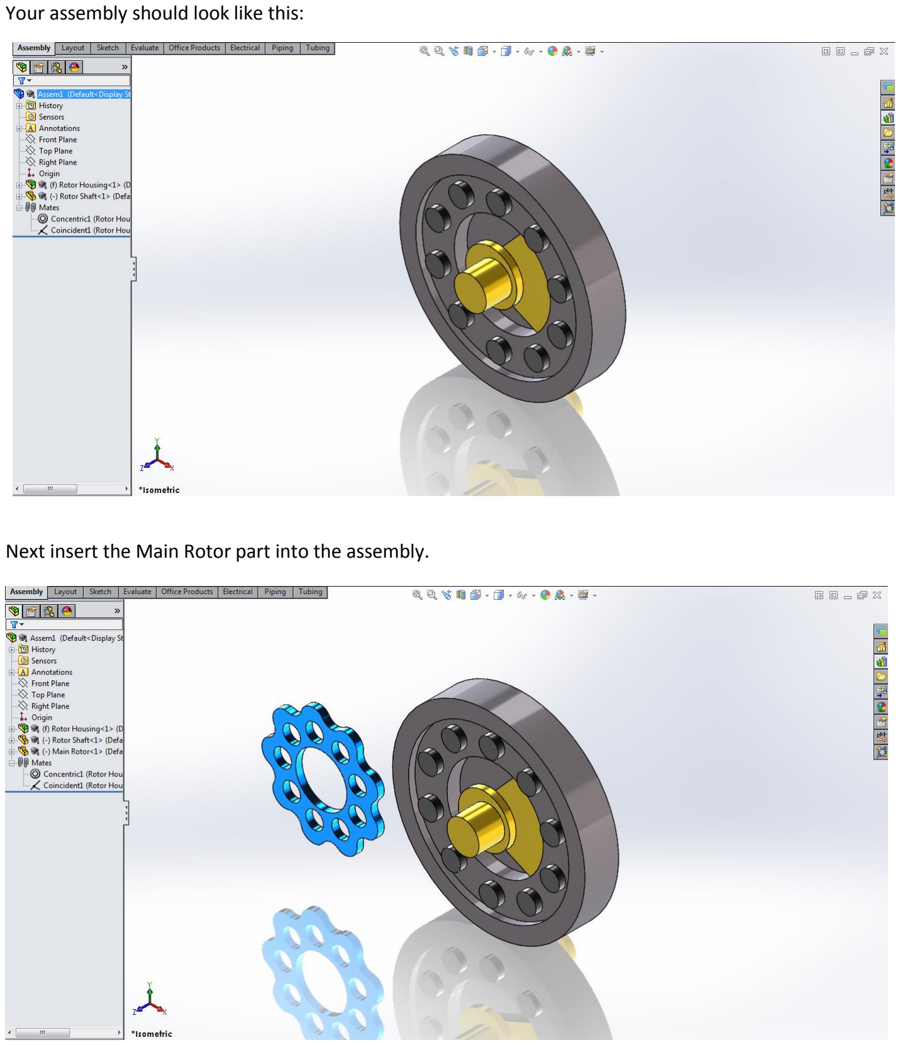
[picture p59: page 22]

Your assembly should look like this:

Next insert the Main Rotor part into the assembly.

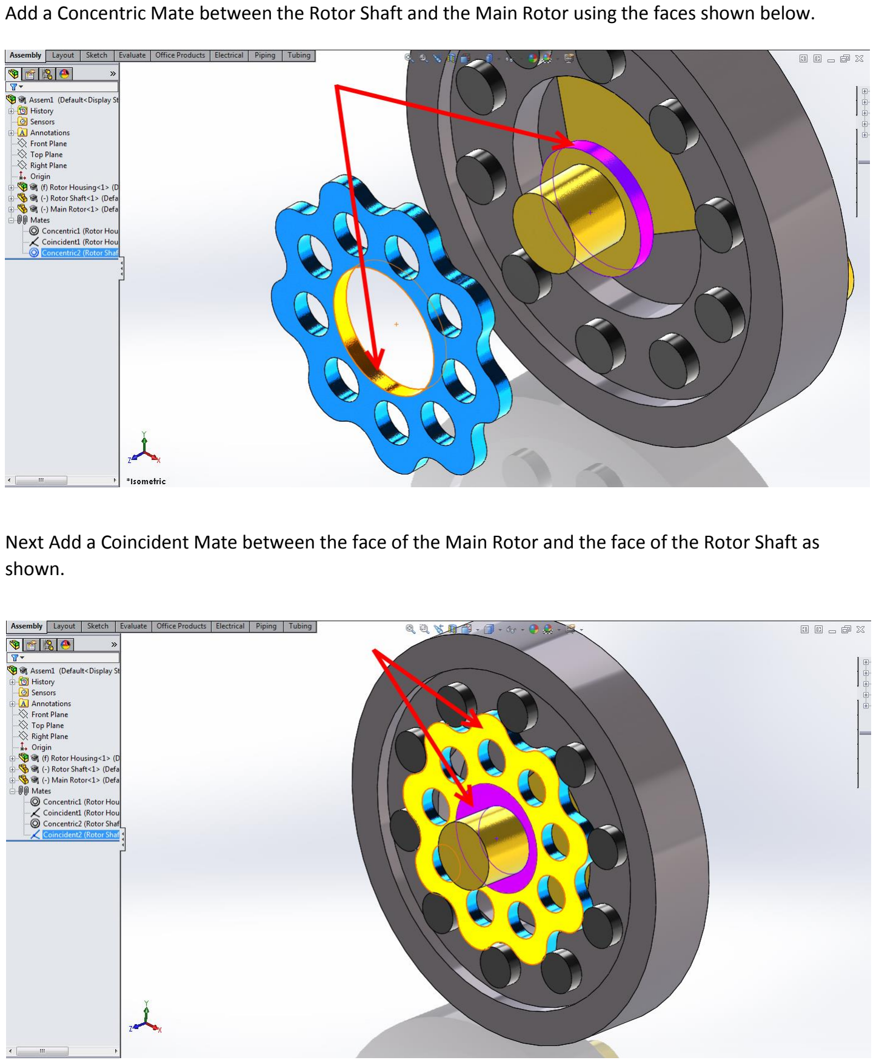
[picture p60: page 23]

Add a Concentric Mate between the Rotor Shaft and the Main Rotor using the faces shown below.

Next Add a Coincident Mate between the face of the Main Rotor and the face of the Rotor Shaft as shown.

Next we are going to add the two mates that give the Cyclodial Drive its motion. It is very important that these mates are done properly as instructed or else the drive will not function correctly.

First Add a CAM mate between the face of the Roller and BOTH outer faces of the Main Rotor as shown:

Rebuild the assembly to make sure the mate was applied properly. If a warning appears, you will have to edit the mate and flip the mate direction.

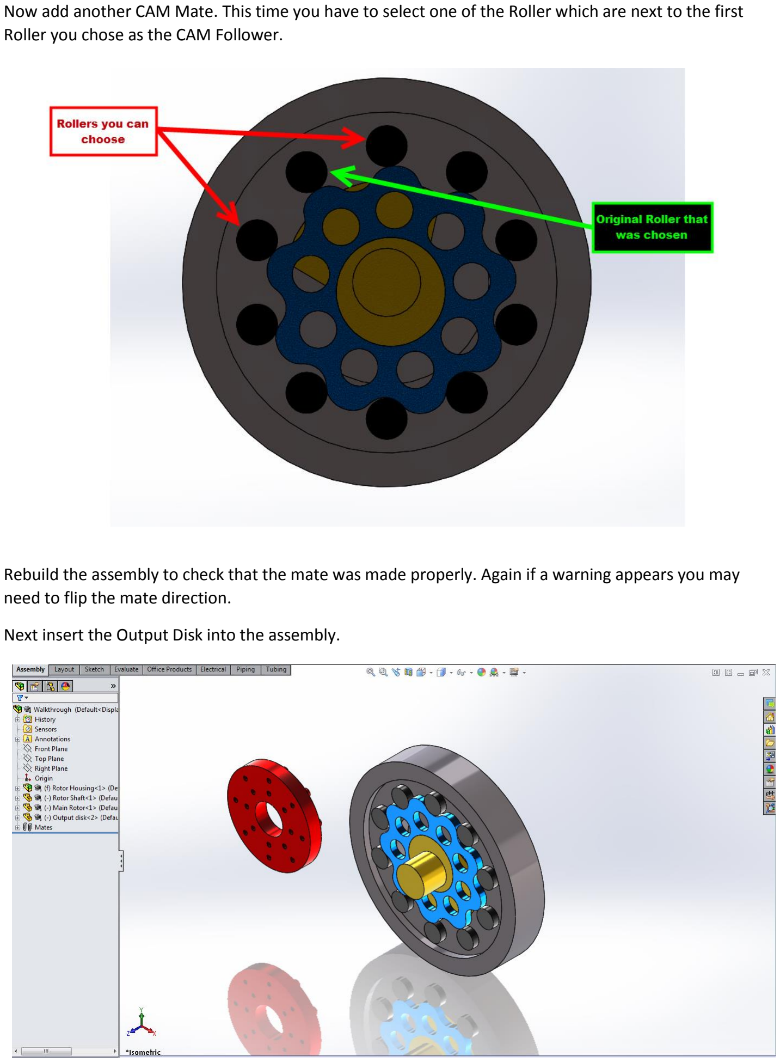
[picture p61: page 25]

Now add another CAM Mate. This time you have to select one of the Roller which are next to the first Roller you chose as the CAM Follower.

Rebuild the assembly to check that the mate was made properly. Again if a warning appears you may need to flip the mate direction.

Next insert the Output Disk into the assembly.

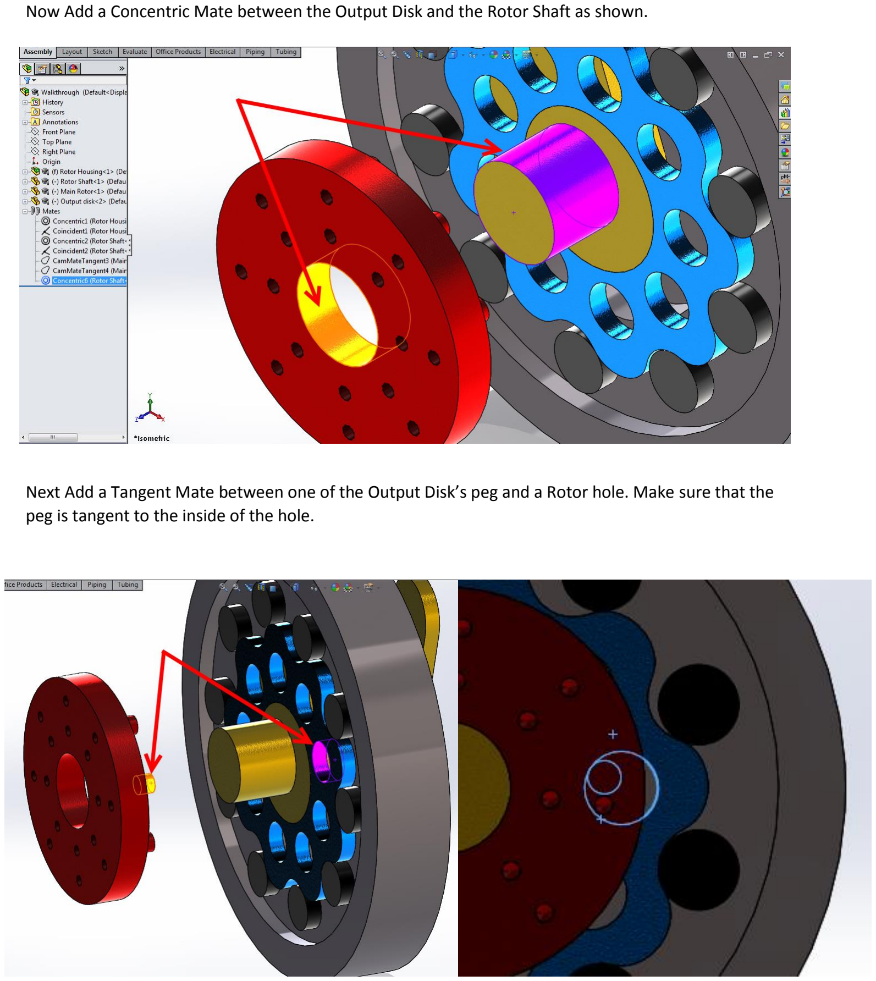
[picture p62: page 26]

Now Add a Concentric Mate between the Output Disk and the Rotor Shaft as shown.

Next Add a Tangent Mate between one of the Output Disk’s peg and a Rotor hole. Make sure that the peg is tangent to the inside of the hole.

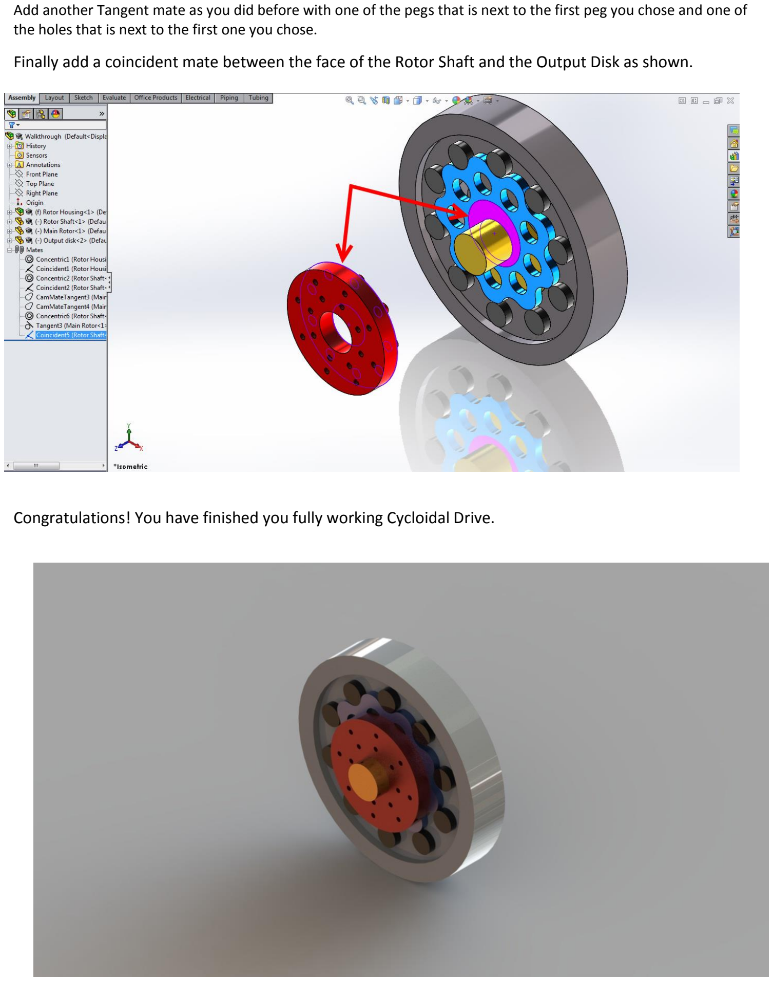
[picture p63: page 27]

Add another Tangent mate as you did before with one of the pegs that is next to the first peg you chose and one of the holes that is next to the first one you chose.

Finally add a coincident mate between the face of the Rotor Shaft and the Output Disk as shown.

Congratulations! You have finished you fully working Cycloidal Drive.

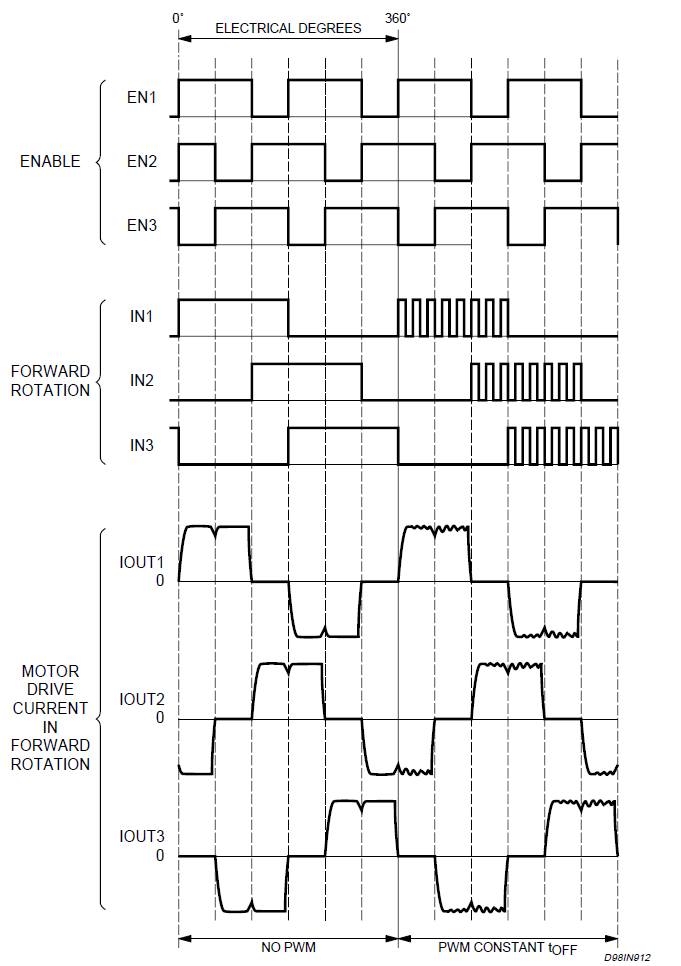
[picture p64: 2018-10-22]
docs/images/electronics/BLDC 6 step sequence.png

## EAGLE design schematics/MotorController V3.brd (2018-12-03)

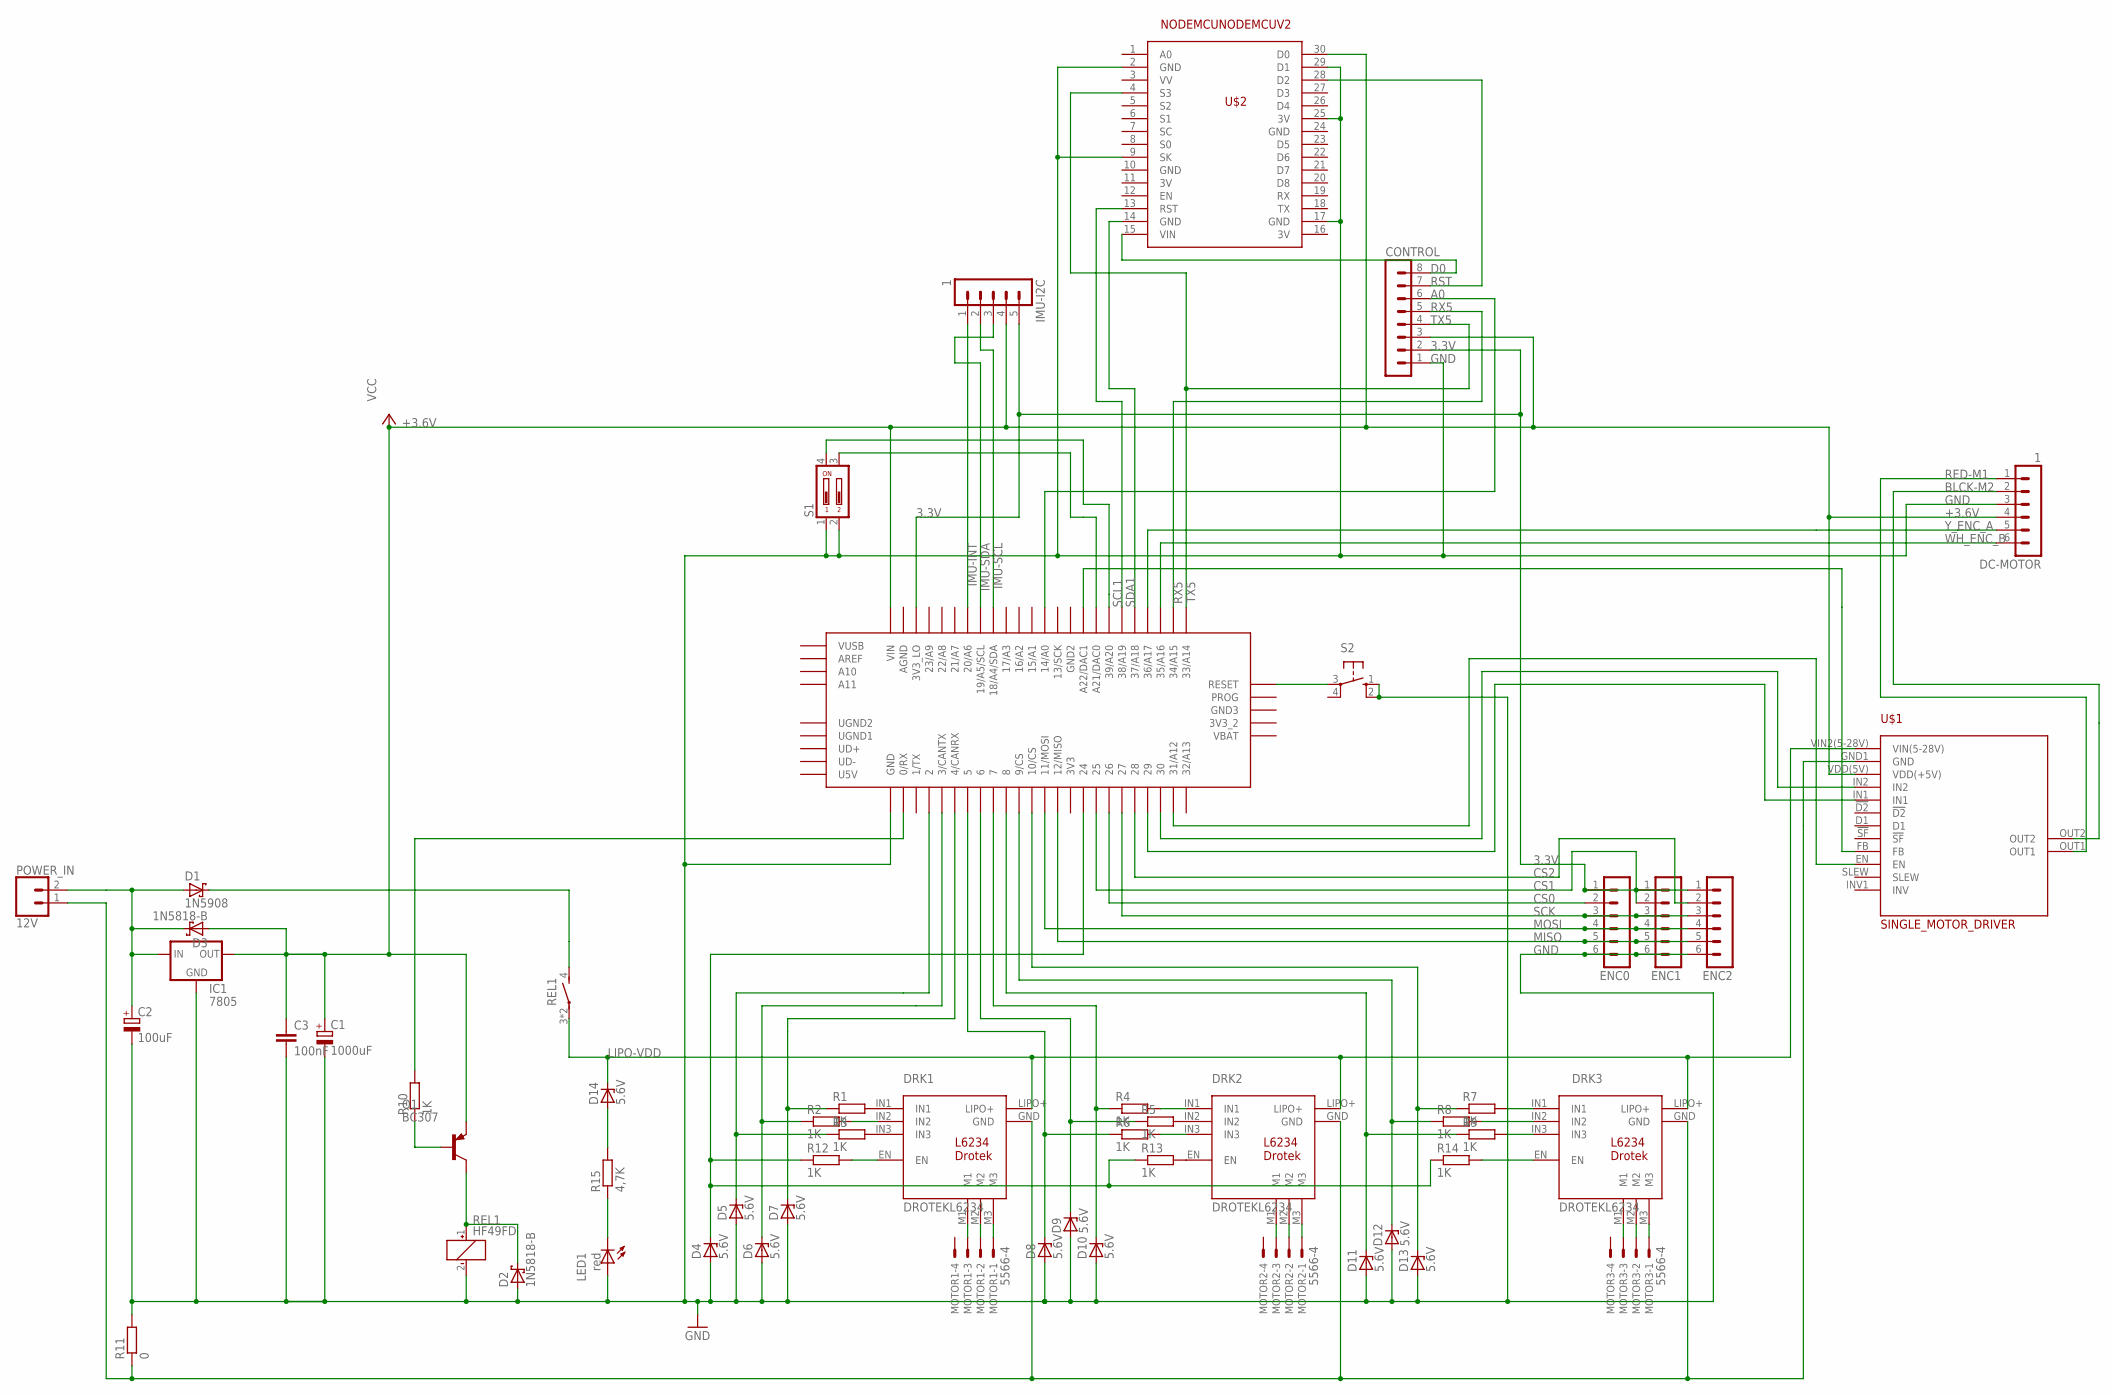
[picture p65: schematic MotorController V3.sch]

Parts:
C1: 1000uF; E2,5-6
C2: 100uF; E5-5
C3: 100nF; C2.5-2
CONTROL: MA08-1
D1: 1N5908; C4111-15
D2, D3: 1N5818-B; DO41-7.6
D4, D5, D6, D7, D8, D9, D10, D11, D12, D13, D14: 5.6V; DO41Z10
DC-MOTOR: 1; MA06-1
DRK1, DRK2, DRK3: DROTEKL6234
ENC0, ENC1, ENC2: MA06-1
IC1: 7805; 78XXS
IMU-I2C: 1; MA05-1
LED1: red; LED3MM
MOTOR1, MOTOR2, MOTOR3: 5566-4
POWER_IN: 12V; SCREWTERMINAL-3.5MM-2
PRJ1: TEENSY_3.5/3.6
Q1: BC307; TO92
R1, R2, R3, R4, R5, R6, R7, R8, R9, R10, R12, R13, R14: 1K; 0207/10
R11: 0; 0204V
R15: 4,7K; 0207/10
REL1: HF49FD
S1: DIP02YL
S2: B3F-10XX
U$1: SINGLE_MOTOR_DRIVER; MOTOR_DRIVER_MC33926_FOOTPRINT_
U$2: NODEMCUNODEMCUV2; NODEMCUV2

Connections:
3.3V: CONTROL.2, ENC0.1, ENC1.1, ENC2.1, IMU-I2C.5, PRJ1.3V3_LO
3V: U$2.11 (3V), U$2.16 (3V)
+3.6V: C1.+, C3.1, CONTROL.3, D3.A, DC-MOTOR.4, IC1.OUT, IMU-I2C.4, PRJ1.VIN, Q1.1 (E), U$1.VDD(5V) (VDD(+5V)), U$2.30 (D0)
A0: CONTROL.6, PRJ1.14/A0
BLCK-M2: DC-MOTOR.2, U$1.OUT2
CS0: ENC0.2, PRJ1.26
CS1: ENC1.2, PRJ1.25
CS2: ENC2.2, PRJ1.28
D0: CONTROL.8, U$2.15 (VIN)
GND: C1.-, C2.-, C3.2, CONTROL.1, D2.A, D4.A, D5.A, D6.A, D7.A, D8.A, D9.A, D10.A, D11.A, D12.A, D13.A, DC-MOTOR.3, ENC0.6, ENC1.6, ENC2.6, IC1.GND, LED1.A, PRJ1.GND, R11.2, REL1.2 (-), S1.1, S1.2, S2.1 (S), S2.2 (S1), U$2.2 (GND), U$2.9 (SK), U$2.10 (GND), U$2.17 (GND), U$2.24 (GND), U$2.25 (3V), U$2.29 (D1)
IMU-INT: IMU-I2C.1, PRJ1.20/A6
IMU-SCL: IMU-I2C.2, PRJ1.18/A4/SDA
IMU-SDA: IMU-I2C.3, PRJ1.19/A5/SCL
LIPO-GND: DRK1.GND, DRK2.GND, DRK3.GND, POWER_IN.1, R11.1, U$1.GND1 (GND)
LIPO-VDD: D14.C, DRK1.LIPO+, DRK2.LIPO+, DRK3.LIPO+, REL1.3, REL1.5, U$1.VIN2(5-28V) (VIN(5-28V))
MISO: ENC0.5, ENC1.5, ENC2.5, PRJ1.12/MISO
MOSI: ENC0.4, ENC1.4, ENC2.4, PRJ1.11/MOSI
unnamed: DRK1.M1, MOTOR1.3
unnamed: DRK1.M2, MOTOR1.2
unnamed: DRK1.M3, MOTOR1.1
unnamed: DRK1.IN1, R1.2
unnamed: DRK1.IN2, R2.2
unnamed: DRK1.IN3, R3.2
unnamed: D7.C, PRJ1.4/CANRX, R1.1
unnamed: D6.C, PRJ1.3/CANTX, R2.1
unnamed: D5.C, PRJ1.2, R3.1
unnamed: DRK3.EN, R14.2
unnamed: DRK2.IN1, R4.2
unnamed: PRJ1.21/DAC0 (A21/DAC0), S1.3
unnamed: DRK2.M1, MOTOR2.3
unnamed: DRK2.M2, MOTOR2.2
unnamed: DRK2.M3, MOTOR2.1
unnamed: DRK3.M1, MOTOR3.3
unnamed: DRK3.M2, MOTOR3.2
unnamed: DRK3.M3, MOTOR3.1
unnamed: DRK2.IN2, R5.2
unnamed: DRK2.IN3, R6.2
unnamed: D8.C, PRJ1.5, R6.1
unnamed: D9.C, PRJ1.6, R5.1
unnamed: D10.C, PRJ1.7, R4.1
unnamed: DRK3.IN2, R8.2
unnamed: DRK3.IN1, R7.2
unnamed: DRK3.IN3, R9.2
unnamed: D11.C, PRJ1.8, R9.1
unnamed: D12.C, PRJ1.9/CS, R8.1
unnamed: D13.C, PRJ1.10/CS, R7.1
unnamed: Q1.2 (B), R10.1
unnamed: D2.C, Q1.3 (C), REL1.1 (+)
unnamed: C2.+, D1.A, D3.C, IC1.IN, POWER_IN.2
unnamed: D14.A, R15.2
unnamed: LED1.K (C), R15.1
unnamed: D1.C, REL1.4 (S)
unnamed: PRJ1.39/A20, S1.4
unnamed: PRJ1.0/RX, R10.2
unnamed: DRK1.EN, R12.2
unnamed: PRJ1.29, U$1.IN1
unnamed: PRJ1.31/A12, U$1.EN
unnamed: D4.C, PRJ1.24, R12.1, R13.1, R14.1
unnamed: PRJ1.30, U$1.IN2
unnamed: DRK2.EN, R13.2
unnamed: PRJ1.RESET, S2.3
unnamed: PRJ1.A22/DAC1, U$1.FB
RED-M1: DC-MOTOR.1, U$1.OUT1
RST: CONTROL.7, U$2.28 (D2)
RX5: CONTROL.5, PRJ1.34/A15
SCK: ENC0.3, ENC1.3, ENC2.3, PRJ1.27
SCL1: PRJ1.38/A19, U$2.13 (RST)
SDA1: PRJ1.37/A18, U$2.14 (GND)
TX5: CONTROL.4, PRJ1.33/A14, U$2.4 (S3)
WH_ENC_B: DC-MOTOR.6, PRJ1.35/A16
Y_ENC_A: DC-MOTOR.5, PRJ1.36/A17

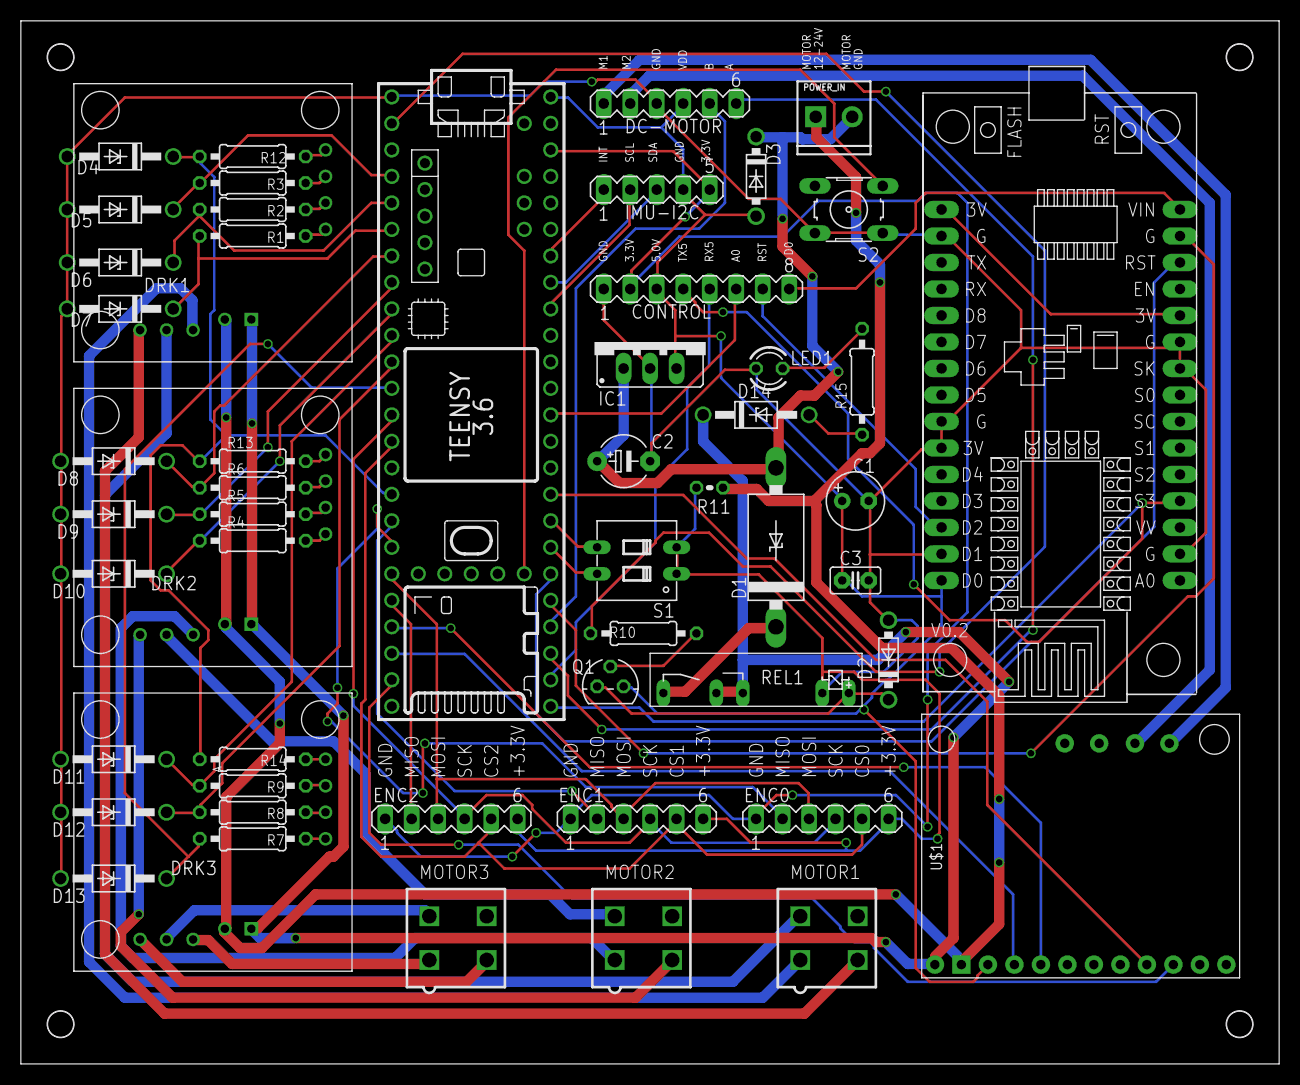
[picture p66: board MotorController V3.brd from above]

Board: 2 copper layers, 120.6 x 100.0 mm, 54 parts (0 on the bottom side), 71 nets.

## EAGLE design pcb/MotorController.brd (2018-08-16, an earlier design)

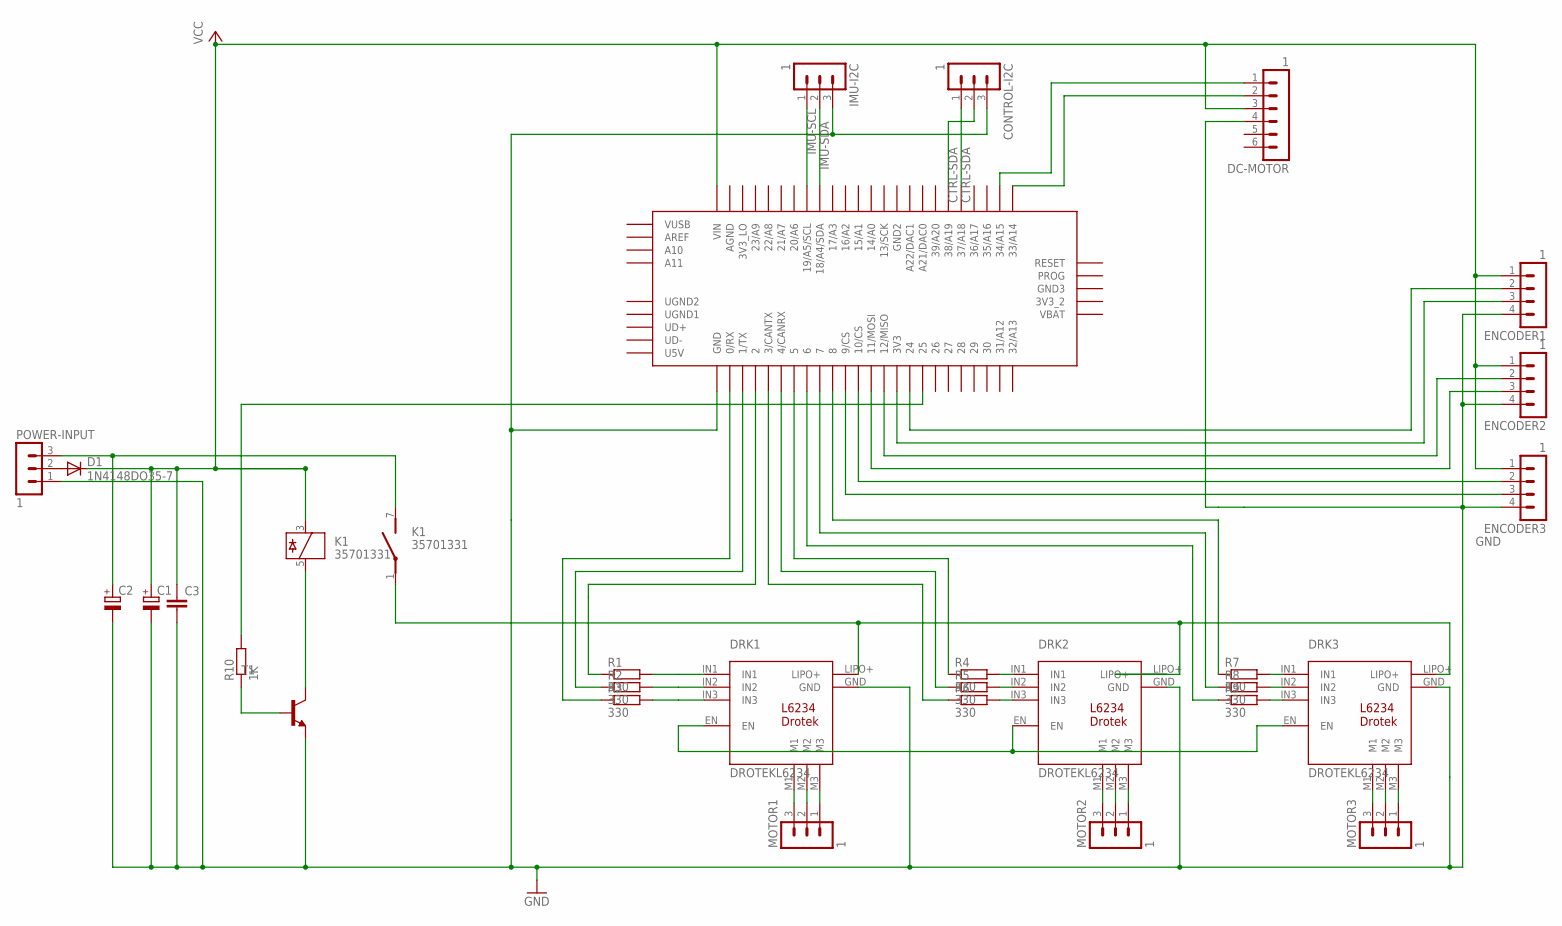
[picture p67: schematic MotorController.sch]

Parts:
C1, C2: CPOL-EUE7.5-16; E7,5-16
C3: C2.5/2; C2.5-2
CONTROL-I2C: 1; MA03-1
D1: 1N4148DO35-7; DO35-7
DC-MOTOR: 1; MA06-1
DRK1, DRK2, DRK3: DROTEKL6234
ENCODER1, ENCODER2, ENCODER3: 1; MA04-1
IMU-I2C: 1; MA03-1
K1: 35701331; REED
MOTOR1, MOTOR2, MOTOR3: 1; MA03-1
POWER-INPUT: 1; MA03-1
PRJ1: TEENSY_3.5/3.6
R1, R2, R3, R4, R5, R6, R7, R8, R9: 330; 0204/7
R10: 1K; 0204/7
T1: -NPN-TO92; TO92

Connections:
CTRL-SDA: CONTROL-I2C.1, PRJ1.37/A18
GND: C1.-, C2.-, C3.2, CONTROL-I2C.3, DC-MOTOR.4, DRK1.GND, DRK2.GND, DRK3.GND, ENCODER1.4, ENCODER2.4, ENCODER3.4, IMU-I2C.3, POWER-INPUT.1, PRJ1.GND, T1.1 (E)
IMU-SCL: IMU-I2C.1, PRJ1.19/A5/SCL
IMU-SDA: IMU-I2C.2, PRJ1.18/A4/SDA
unnamed: DRK1.M1, MOTOR1.3
unnamed: DRK1.M2, MOTOR1.2
unnamed: DRK1.M3, MOTOR1.1
unnamed: DRK1.IN1, R1.2
unnamed: DRK1.IN2, R2.2
unnamed: DRK1.IN3, R3.2
unnamed: PRJ1.2, R1.1
unnamed: PRJ1.1/TX, R2.1
unnamed: PRJ1.0/RX, R3.1
unnamed: DRK1.EN, DRK2.EN, DRK3.EN
unnamed: DRK2.IN1, R4.2
unnamed: DRK1.LIPO+, DRK2.LIPO+, DRK3.LIPO+, K1.1
unnamed: DRK2.M1, MOTOR2.3
unnamed: DRK2.M2, MOTOR2.2
unnamed: DRK2.M3, MOTOR2.1
unnamed: DRK3.M1, MOTOR3.3
unnamed: DRK3.M2, MOTOR3.2
unnamed: DRK3.M3, MOTOR3.1
unnamed: DRK2.IN2, R5.2
unnamed: DRK2.IN3, R6.2
unnamed: PRJ1.3/CANTX, R6.1
unnamed: PRJ1.4/CANRX, R5.1
unnamed: PRJ1.5, R4.1
unnamed: DRK3.IN2, R8.2
unnamed: DRK3.IN1, R7.2
unnamed: DRK3.IN3, R9.2
unnamed: PRJ1.6, R9.1
unnamed: PRJ1.7, R8.1
unnamed: PRJ1.8, R7.1
unnamed: R10.1, T1.2 (B)
unnamed: K1.5, T1.3 (C)
unnamed: C2.+, K1.7 (S), POWER-INPUT.3
unnamed: ENCODER3.3, PRJ1.9/CS
unnamed: ENCODER3.2, PRJ1.10/CS
unnamed: ENCODER2.3, PRJ1.11/MOSI
unnamed: ENCODER2.2, PRJ1.12/MISO
unnamed: ENCODER1.3, PRJ1.3V3
unnamed: ENCODER1.2, PRJ1.24
unnamed: D1.A, POWER-INPUT.2
unnamed: DC-MOTOR.2, PRJ1.33/A14
unnamed: DC-MOTOR.1, PRJ1.34/A15
unnamed: PRJ1.25, R10.2
unnamed: CONTROL-I2C.2, PRJ1.38/A19
VCC: C1.+, C3.1, D1.C, DC-MOTOR.3, ENCODER1.1, ENCODER2.1, ENCODER3.1, K1.3, PRJ1.VIN

Board: 2 copper layers, 30 parts (0 on the bottom side), 48 nets, no tracks yet.

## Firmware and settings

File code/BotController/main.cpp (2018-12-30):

#include "Arduino.h"
#include <libraries/I2CSlave.h>

#include <BrushlessMotorDriver.h>
#include "Engine.h"
#include "BotController.h"

#include <PatternBlinker.h>
#include <BotMemory.h>

#include <common.h>

static uint8_t DefaultPattern[3] = { 0b11001000, 0b00001100, 0b10000000 };	// nice!

PatternBlinker ledBlinker(LED_PIN, 50 /* ms */); // one bit in the patterns above is active for 100ms

HardwareSerial* logger = &Serial5;			// UART used to log


i2c_t3* Wires[3] = { &Wire, &Wire1, &Wire2};
i2c_t3* IMUWire = NULL;

I2CSlave* i2cSlave = new I2CSlave(&Wire1);

void setup()
{
	logger->begin(460800);
	uint32_t now = millis();

	// let the LED blink two times to indicate startup
	digitalWrite(LED_PIN,LOW);
	delay(30);
	digitalWrite(LED_PIN,HIGH);
	delay(30);
	digitalWrite(LED_PIN,LOW);
	delay(30);
	digitalWrite(LED_PIN,HIGH);
	delay(30);
	digitalWrite(LED_PIN,LOW);
	ledBlinker.set(DefaultPattern,sizeof(DefaultPattern));

	// initialize configuration values coming from EEPROM
	memory.setup();

	// join the i2c bus with the webserver
	i2cSlave->setup();

	// this takes 3.5s seconds (mainly due to IMU initialization)
	BotController::getInstance()->setup();

	// initialize LED_PIN after BotController::getInstance()->setup()
	// since SPI does use it default wise for SCK, but this is remapped
	pinMode(LED_PIN, OUTPUT);

	logger->print("BotController - h for help ");
	logger->print(millis()-now);
	logger->print("ms setup time");
	logger->println();
}

void loop()
{
	ledBlinker.loop(millis());    				// LED on Teensy board and LED on power switch
	BotController::getInstance()->loop();		// do the balancing business
	i2cSlave->loop();							// execute commands from webserver that came in via I2C
	memory.loop(millis());						// check if something happened in memory that is to be saved in EEPROM
}

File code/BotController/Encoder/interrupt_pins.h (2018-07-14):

// interrupt pins for known boards

// Teensy (and maybe others) define these automatically
#if !defined(CORE_NUM_INTERRUPT)

// Wiring boards
#if defined(WIRING)
  #define CORE_NUM_INTERRUPT	NUM_EXTERNAL_INTERRUPTS
  #if NUM_EXTERNAL_INTERRUPTS > 0
  #define CORE_INT0_PIN		EI0
  #endif
  #if NUM_EXTERNAL_INTERRUPTS > 1
  #define CORE_INT1_PIN		EI1
  #endif
  #if NUM_EXTERNAL_INTERRUPTS > 2
  #define CORE_INT2_PIN		EI2
  #endif
  #if NUM_EXTERNAL_INTERRUPTS > 3
  #define CORE_INT3_PIN		EI3
  #endif
  #if NUM_EXTERNAL_INTERRUPTS > 4
  #define CORE_INT4_PIN		EI4
  #endif
  #if NUM_EXTERNAL_INTERRUPTS > 5
  #define CORE_INT5_PIN		EI5
  #endif
  #if NUM_EXTERNAL_INTERRUPTS > 6
  #define CORE_INT6_PIN		EI6
  #endif
  #if NUM_EXTERNAL_INTERRUPTS > 7
  #define CORE_INT7_PIN		EI7
  #endif

// Arduino Uno, Duemilanove, Diecimila, LilyPad, Mini, Fio, etc...
#elif defined(__AVR_ATmega328P__) || defined(__AVR_ATmega168__) || defined(__AVR_ATmega8__)
  #define CORE_NUM_INTERRUPT	2
  #define CORE_INT0_PIN		2
  #define CORE_INT1_PIN		3

// Arduino Mega
#elif defined(__AVR_ATmega1280__) || defined(__AVR_ATmega2560__)
  #define CORE_NUM_INTERRUPT	6
  #define CORE_INT0_PIN		2
  #define CORE_INT1_PIN		3
  #define CORE_INT2_PIN		21
  #define CORE_INT3_PIN		20
  #define CORE_INT4_PIN		19
  #define CORE_INT5_PIN		18

// Arduino Leonardo (untested)
#elif defined(__AVR_ATmega32U4__) && !defined(CORE_TEENSY)
  #define CORE_NUM_INTERRUPT	5
  #define CORE_INT0_PIN		3
  #define CORE_INT1_PIN		2
  #define CORE_INT2_PIN		0
  #define CORE_INT3_PIN		1
  #define CORE_INT4_PIN		7

// Sanguino (untested)
#elif defined(__AVR_ATmega644P__) || defined(__AVR_ATmega644__)
  #define CORE_NUM_INTERRUPT	3
  #define CORE_INT0_PIN		10
  #define CORE_INT1_PIN		11
  #define CORE_INT2_PIN		2

// Chipkit Uno32 - attachInterrupt may not support CHANGE option
#elif defined(__PIC32MX__) && defined(_BOARD_UNO_)
  #define CORE_NUM_INTERRUPT	5
  #define CORE_INT0_PIN		38
  #define CORE_INT1_PIN		2
  #define CORE_INT2_PIN		7
  #define CORE_INT3_PIN		8
  #define CORE_INT4_PIN		35

// Chipkit Uno32 - attachInterrupt may not support CHANGE option
#elif defined(__PIC32MX__) && defined(_BOARD_MEGA_)
  #define CORE_NUM_INTERRUPT	5
  #define CORE_INT0_PIN		3
  #define CORE_INT1_PIN		2
  #define CORE_INT2_PIN		7
  #define CORE_INT3_PIN		21
  #define CORE_INT4_PIN		20

// http://hlt.media.mit.edu/?p=1229
#elif defined(__AVR_ATtiny45__) || defined(__AVR_ATtiny85__)
  #define CORE_NUM_INTERRUPT    1
  #define CORE_INT0_PIN		2

//https://github.com/SpenceKonde/ATTinyCore/blob/master/avr/extras/ATtiny_x313.md
#elif defined(__AVR_ATtinyX313__)
  #define CORE_NUM_INTERRUPT    2
  #define CORE_INT0_PIN		4
  #define CORE_INT1_PIN		5

// Attiny167 same core as abobe
#elif defined(__AVR_ATtiny167__)
  #define CORE_NUM_INTERRUPT	2
  #define CORE_INT0_PIN		14
  #define CORE_INT1_PIN		3


// Arduino Due
#elif defined(__SAM3X8E__)
  #define CORE_NUM_INTERRUPT	54
  #define CORE_INT0_PIN		0
  #define CORE_INT1_PIN		1
  #define CORE_INT2_PIN		2
  #define CORE_INT3_PIN		3
  #define CORE_INT4_PIN		4
  #define CORE_INT5_PIN		5
  #define CORE_INT6_PIN		6
  #define CORE_INT7_PIN		7
  #define CORE_INT8_PIN		8
  #define CORE_INT9_PIN		9
  #define CORE_INT10_PIN	10
  #define CORE_INT11_PIN	11
  #define CORE_INT12_PIN	12
  #define CORE_INT13_PIN	13
  #define CORE_INT14_PIN	14
  #define CORE_INT15_PIN	15
  #define CORE_INT16_PIN	16
  #define CORE_INT17_PIN	17
  #define CORE_INT18_PIN	18
  #define CORE_INT19_PIN	19
  #define CORE_INT20_PIN	20
  #define CORE_INT21_PIN	21
  #define CORE_INT22_PIN	22
  #define CORE_INT23_PIN	23
  #define CORE_INT24_PIN	24
  #define CORE_INT25_PIN	25
  #define CORE_INT26_PIN	26
  #define CORE_INT27_PIN	27
  #define CORE_INT28_PIN	28
  #define CORE_INT29_PIN	29
  #define CORE_INT30_PIN	30
  #define CORE_INT31_PIN	31
  #define CORE_INT32_PIN	32
  #define CORE_INT33_PIN	33
  #define CORE_INT34_PIN	34
  #define CORE_INT35_PIN	35
  #define CORE_INT36_PIN	36
  #define CORE_INT37_PIN	37
  #define CORE_INT38_PIN	38
  #define CORE_INT39_PIN	39
  #define CORE_INT40_PIN	40
  #define CORE_INT41_PIN	41
  #define CORE_INT42_PIN	42
  #define CORE_INT43_PIN	43
  #define CORE_INT44_PIN	44
  #define CORE_INT45_PIN	45
  #define CORE_INT46_PIN	46
  #define CORE_INT47_PIN	47
  #define CORE_INT48_PIN	48
  #define CORE_INT49_PIN	49
  #define CORE_INT50_PIN	50
  #define CORE_INT51_PIN	51
  #define CORE_INT52_PIN	52
  #define CORE_INT53_PIN	53
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

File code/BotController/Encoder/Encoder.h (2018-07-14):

/* Encoder Library, for measuring quadrature encoded signals
 * http://www.pjrc.com/teensy/td_libs_Encoder.html
 * Copyright (c) 2011,2013 PJRC.COM, LLC - Paul Stoffregen <paul@pjrc.com>
 *
 * Version 1.2 - fix -2 bug in C-only code
 * Version 1.1 - expand to support boards with up to 60 interrupts
 * Version 1.0 - initial release
 *
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
 * THE SOFTWARE IS PROVIDED "AS IS", WITHOUT WARRANTY OF ANY KIND, EXPRESS OR
 * IMPLIED, INCLUDING BUT NOT LIMITED TO THE WARRANTIES OF MERCHANTABILITY,
 * FITNESS FOR A PARTICULAR PURPOSE AND NONINFRINGEMENT. IN NO EVENT SHALL THE
 * AUTHORS OR COPYRIGHT HOLDERS BE LIABLE FOR ANY CLAIM, DAMAGES OR OTHER
 * LIABILITY, WHETHER IN AN ACTION OF CONTRACT, TORT OR OTHERWISE, ARISING FROM,
 * OUT OF OR IN CONNECTION WITH THE SOFTWARE OR THE USE OR OTHER DEALINGS IN
 * THE SOFTWARE.
 */


#ifndef Encoder_h_
#define Encoder_h_

#if defined(ARDUINO) && ARDUINO >= 100
#include "Arduino.h"
#elif defined(WIRING)
#include "Wiring.h"
#else
#include "WProgram.h"
#include "pins_arduino.h"
#endif

#include "Encoder/direct_pin_read.h"

#if defined(ENCODER_USE_INTERRUPTS) || !defined(ENCODER_DO_NOT_USE_INTERRUPTS)
#define ENCODER_USE_INTERRUPTS
#define ENCODER_ARGLIST_SIZE CORE_NUM_INTERRUPT
#include "Encoder/interrupt_pins.h"
#ifdef ENCODER_OPTIMIZE_INTERRUPTS
#include "Encoder/interrupt_config.h"
#endif
#else
#define ENCODER_ARGLIST_SIZE 0
#endif



// All the data needed by interrupts is consolidated into this ugly struct
// to facilitate assembly language optimizing of the speed critical update.
// The assembly code uses auto-incrementing addressing modes, so the struct
// must remain in exactly this order.
typedef struct {
	volatile IO_REG_TYPE * pin1_register;
	volatile IO_REG_TYPE * pin2_register;
	IO_REG_TYPE            pin1_bitmask;
	IO_REG_TYPE            pin2_bitmask;
	uint8_t                state;
	int32_t                position;
} Encoder_internal_state_t;

class Encoder
{
public:
	Encoder(uint8_t pin1, uint8_t pin2) {
		#ifdef INPUT_PULLUP
		pinMode(pin1, INPUT_PULLUP);
		pinMode(pin2, INPUT_PULLUP);
		#else
		pinMode(pin1, INPUT);
		digitalWrite(pin1, HIGH);
		pinMode(pin2, INPUT);
		digitalWrite(pin2, HIGH);
		#endif
		encoder.pin1_register = PIN_TO_BASEREG(pin1);
		encoder.pin1_bitmask = PIN_TO_BITMASK(pin1);
		encoder.pin2_register = PIN_TO_BASEREG(pin2);
		encoder.pin2_bitmask = PIN_TO_BITMASK(pin2);
		encoder.position = 0;
		// allow time for a passive R-C filter to charge
		// through the pullup resistors, before reading
		// the initial state
		delayMicroseconds(2000);
		uint8_t s = 0;
		if (DIRECT_PIN_READ(encoder.pin1_register, encoder.pin1_bitmask)) s |= 1;
		if (DIRECT_PIN_READ(encoder.pin2_register, encoder.pin2_bitmask)) s |= 2;
		encoder.state = s;
#ifdef ENCODER_USE_INTERRUPTS
		interrupts_in_use = attach_interrupt(pin1, &encoder);
		interrupts_in_use += attach_interrupt(pin2, &encoder);
#endif
		//update_finishup();  // to force linker to include the code (does not work)
	}


#ifdef ENCODER_USE_INTERRUPTS
	inline int32_t read() {
		if (interrupts_in_use < 2) {
			noInterrupts();
			update(&encoder);
		} else {
			noInterrupts();
		}
		int32_t ret = encoder.position;
		interrupts();
		return ret;
	}
	inline void write(int32_t p) {
		noInterrupts();
		encoder.position = p;
		interrupts();
	}
#else
	inline int32_t read() {
		update(&encoder);
		return encoder.position;
	}
	inline void write(int32_t p) {
		encoder.position = p;
	}
#endif
private:
	Encoder_internal_state_t encoder;
#ifdef ENCODER_USE_INTERRUPTS
	uint8_t interrupts_in_use;
#endif
public:
	static Encoder_internal_state_t * interruptArgs[ENCODER_ARGLIST_SIZE];

//                           _______         _______
//               Pin1 ______|       |_______|       |______ Pin1
// negative <---         _______         _______         __      --> positive
//               Pin2 __|       |_______|       |_______|   Pin2

		//	new	new	old	old
		//	pin2	pin1	pin2	pin1	Result
		//	----	----	----	----	------
		//	0	0	0	0	no movement
		//	0	0	0	1	+1
		//	0	0	1	0	-1
		//	0	0	1	1	+2  (assume pin1 edges only)
		//	0	1	0	0	-1
		//	0	1	0	1	no movement
		//	0	1	1	0	-2  (assume pin1 edges only)
		//	0	1	1	1	+1
		//	1	0	0	0	+1
		//	1	0	0	1	-2  (assume pin1 edges only)
		//	1	0	1	0	no movement
		//	1	0	1	1	-1
		//	1	1	0	0	+2  (assume pin1 edges only)
		//	1	1	0	1	-1
		//	1	1	1	0	+1
		//	1	1	1	1	no movement
/*
	// Simple, easy-to-read "documentation" version :-)
	//
	void update(void) {
		uint8_t s = state & 3;
		if (digitalRead(pin1)) s |= 4;
		if (digitalRead(pin2)) s |= 8;
		switch (s) {
			case 0: case 5: case 10: case 15:
				break;
			case 1: case 7: case 8: case 14:
				position++; break;
			case 2: case 4: case 11: case 13:
				position--; break;
			case 3: case 12:
				position += 2; break;
			default:
				position -= 2; break;
		}
		state = (s >> 2);
	}
*/
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

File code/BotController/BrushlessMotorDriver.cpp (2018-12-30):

/*
 * BLDCController.cpp
 *
 *  Created on: 29.07.2018
 *      Author: JochenAlt
 */

#include <Arduino.h>
#include <setup.h>
#include <libraries/Util.h>
#include <BotMemory.h>
#include <BrushlessMotorDriver.h>

#include <TimePassedBy.h>

const float maxAngleError = radians(10);						// limit for PID controller
const float minTorqueRatio = 0.1;								// minimum percentage of torque when in position
const float maxAdvancePhaseAngle = radians(10);					// maximum phase between voltage and current due to EMF
const float RevPerSecondPerVolt = 4;							// motor constant of Maxon EC max 40 W
const float voltage = 20;										// [V] coming from the battery to server the motors
const float maxRevolutionSpeed = voltage*RevPerSecondPerVolt; 	// [rev/s]


MotorConfig& motorConfig = memory.persistentMem.motorControllerConfig;

// array to store pre-computed values of space vector wave form (SVPWM)
// array size is choosen by having a maximum difference of 1% in two subsequent table items,
// i.e. we have a precision of 1%. The rest is compensated by the optical
// encoder with a precision of 0.1%
#define svpwmArraySize 244 // manually set such that two adjacent items have a difference of 2 of 255 at most (approx. 1%)
int svpwmTable[svpwmArraySize];

void setPwmTable(int i, int value) {
	if ((i<0) || (i> svpwmArraySize))
		fatalError("pwmTable:Idx out of bound");
	svpwmTable[i] = value;
}

int getPwmTable(int i) {
	if ((i<0) || (i> svpwmArraySize))
		fatalError("pwmTable:Idx out of bound");
	return svpwmTable[i];
}

void precomputeSVPMWave() {
	const int maxPWMValue = (1<<pwmResolutionBits)-1;
	const float spaceVectorScaleUpFactor = 1.15; // empiric value to reach full pwm scale
	static boolean initialized = false;
	if (!initialized) {
		for (int i = 0;i<svpwmArraySize;i++) {
			float angle = float(i) / float(svpwmArraySize) * (TWO_PI);
			float phaseA = sin(angle);
			float phaseB = sin(angle + M_PI*2.0/3.0);
			float phaseC = sin(angle + M_PI*4.0/3.0);

			// trick to avoid the switch of 6 phases everyone else is doing, neat, huh?
			float voff = (min(phaseA, min(phaseB, phaseC)) + max(phaseA, max(phaseB, phaseC)))/2.0;
			setPwmTable(i,(phaseA - voff)/2.0*spaceVectorScaleUpFactor*maxPWMValue);

			// if you want to use plain sin waves:
			setPwmTable(i,(phaseA/2.0 + 0.5)*maxPWMValue);
		}
		initialized = true;
	}
}



void MotorConfig::initDefaultValues() {
	// at slow speeds PID controller is aggressively keeping the position
	pid_position.Kp = 0.1;
	pid_position.Ki = 0.1;
	pid_position.Kd = 0.0000;

	pid_speed.Kp = 0.1;
	pid_speed.Ki = 0.1;
	pid_speed.Kd = 0.001;

	pid_lifter.Kp = 0.01;
	pid_lifter.Ki = 0.005;
	pid_lifter.Kd = 0.0;

	phaseAAngle[0] = radians(228);
	phaseAAngle[1] = radians(230);
	phaseAAngle[2] = radians(127);
}

void MotorConfig::print() {
	loggingln("motor controller configuration:");
	logging("   PID (speed=0)  : ");
	logging("(");
	logging(pid_position.Kp,3);
	logging(",");
	logging(pid_position.Ki,3);
	logging(",");
	logging(pid_position.Kd,4);
	loggingln(")");
	logging("   PID (speed=max): ");
	logging("(");
	logging(pid_speed.Kp,3);
	logging(",");
	logging(pid_speed.Ki,3);
	logging(",");
	logging(pid_speed.Kd,4);
	loggingln(")");
	logging("   motorID=(");
	logging(MotorSequenceIdx[0]);
	logging(",");
	logging(MotorSequenceIdx[1]);
	logging(",");
	logging(MotorSequenceIdx[2]);
	loggingln(")");
	logging("   rotorAngle=(");
	logging(degrees(phaseAAngle[0]),1);
	logging(",");
	logging(degrees(phaseAAngle[1]),1);
	logging(",");
	logging(degrees(phaseAAngle[2]),1);
	loggingln(")");
	loggingln("lifter controller configuration:");
	logging("   PID (speed=max): ");
	logging("(");
	logging(pid_lifter.Kp);
	logging(",");
	logging(pid_lifter.Ki);
	logging(",");
	logging(pid_lifter.Kd);
	loggingln(")");
}


int BrushlessMotorDriver::getPWMValue(float torque, float angle_rad) {
	// map input angle to 0..2*PI

	// clear negative angles (fmod does not do this)
	if (angle_rad < 0)
		angle_rad += ((int)(-angle_rad/TWO_PI + 1.0))*TWO_PI;

	angle_rad = fmod(angle_rad, TWO_PI);

	// compute index in precomputed pwm array
	int angleIndex = ((int)(angle_rad / TWO_PI * svpwmArraySize));
	if ((angleIndex < 0) || (angleIndex > svpwmArraySize))
		fatalError("getPWMValue: idx out of bounds");

	return  torque * getPwmTable(angleIndex);
}

BrushlessMotorDriver::BrushlessMotorDriver() {
	// initialize precomputed spvm values
	// first invocation does the initialization
	precomputeSVPMWave();
}

void BrushlessMotorDriver::setup( int motorNo, MenuController* menuCtrl, bool reverse) {
	this->motorNo = motorNo;
	this->reverse = reverse;
	registerMenuController(menuCtrl);

	// initialize SPI bus used to communicate with AS5047D magnetic encoders
	// (this is done once only)
	AS5047D::setupBus(MOSI_PIN, MISO_PIN, SCK_PIN, SS_PIN);

}

void BrushlessMotorDriver::setupMotor(int EnablePin, int Input1Pin, int Input2Pin, int Input3Pin) {
	// there's only one enable pin that has a short cut to EN1, EN2, and EN3 from L6234
	enablePin = EnablePin;

	input1Pin = Input1Pin;
	input2Pin = Input2Pin;
	input3Pin = Input3Pin;

	// setup L6234 input PWM pins
	analogWriteResolution(pwmResolutionBits);

	// choose a frequency that just can't be heard
	analogWriteFrequency(input1Pin, 30000);
	analogWriteFrequency(input2Pin, 30000);
	analogWriteFrequency(input3Pin, 30000);

	// these pins have to have PWM functionality
	pinMode(input1Pin, OUTPUT);
	pinMode(input1Pin, OUTPUT);
	pinMode(input1Pin, OUTPUT);

	// enable all enable lines at once (Drotek L6234 board has all enable lines connected)
	pinMode(enablePin, OUTPUT);
	digitalWrite(enablePin, LOW); // start with disabled motor, ::enable turns it on
}

void BrushlessMotorDriver::setupEncoder(uint8_t clientSelectPin) {

	// initialize SPI's CS
	magEncoder.setup(clientSelectPin);

	if (abs(magEncoder.getSensorRead() - TWO_PI) < floatPrecision) {
		logging("Encoder ");
		logging(motorNo);
		logging(" does not return a value");
		fatalError("Encoder fail");
	}
}

// the motor is supposed to follow the reference angle as close as possible
void BrushlessMotorDriver::turnReferenceAngle(float dT) {
	float accel = (targetMotorSpeed - currentReferenceMotorSpeed)/dT;
	if (abs(accel) > MaxWheelAcceleration)
		accel = sgn(accel) * MaxWheelAcceleration;

	currentReferenceMotorSpeed += accel*dT;
	currentReferenceMotorSpeed = constrain(currentReferenceMotorSpeed, -maxRevolutionSpeed, + maxRevolutionSpeed);
	referenceAngle += currentReferenceMotorSpeed * TWO_PI * dT;
	referenceAngle = constrain(referenceAngle, getEncoderAngle() - radians(45), getEncoderAngle() + radians(45));
}

void BrushlessMotorDriver::reset() {
	targetMotorSpeed = 0;
	magEncoder.reset();
	readEncoderAngle();
	magneticFieldAngle = getEncoderAngle();	 // [rad] angle of the induced magnetic field
	referenceAngle = magneticFieldAngle;

	currentReferenceMotorSpeed = 0;		// [rev/s]
	measuredMotorSpeed = 0;				// [rev/s]
	measurementAngle = 0;
	pid.reset();
	timeLoop.init();
}
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

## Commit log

2018-06-25 omniwheel with mounting hub
    [CircularSpline.ipt, HarmonicDrive-WaveGenerator-Bottom.ipt, HarmonicDrive-WaveGenerator.ipt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]
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2018-06-27 0.25 more space between rolls and spoke
    [Antriebsstrang.iam, HarmonicDrive.iam, HarmonicDrive.ipt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]
2018-06-30 Friction surface of omniwheel rols adapted
    [050579405.ipt, Antriebsstrang.iam, Avago Encoder.iam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]
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2018-07-01 print of omniwheel with space for corund
    [CircularSpline.ipt, Drive.iam, DriveChain.iam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]
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2018-07-07 built and corrected omniwheel
    [OmniWheel.ipt, OmniWheelBigRoll.stl, OmniWheelBottomLid.stl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]
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2018-07-13 enlarged bearings in planetary gear
    [050579405.ipt, Avago Encoder.iam, Baugruppe5.iam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]
2018-07-14 corrected big rolls in Omni wheels (tighter bearing space)
    [Bom.xlsx, DriveChain.iam, OmniWheel.ipt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]
2018-07-14 fixed and centered encoder within enclosure
    [Avago Encoder.iam, Drive.iam, DriveChain.iam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]
2018-07-15 planetary Gear bearing correction
    [Avago Encoder.iam, Bom.xlsx, DriveChain.iam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]
2018-07-16 back to helical gearing
    [InsideGear.stl, PlanetGear.stl, PlanetaryGear.iam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]
2018-07-16 replace old enclosure by leaner shape
    [Avago Encoder.iam, Drive.iam, DriveChain.iam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]
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2018-07-18 Revert "adapted teeth shape"
    This reverts commit 82a1961c36844213699828fc2cebeaf81ce44edd.
    [Drive.iam, DriveChain.iam, InsideGear.stl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]
2018-07-18 Revert "Revert "adapted teeth shape""
    This reverts commit 169dd93047d1f5d752c282b07249b5d372d47a6e.
    [Drive.iam, DriveChain.iam, InsideGear.stl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]
2018-07-18 made planetary gear wider
    [Drive.iam, DriveChain.iam, DriveChainEnclosure.ipt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]
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2018-07-21 increased modul to 1.0 of planetary gear
    [GearConstruction.iam, InsideGear.stl, PlanetGear.stl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]
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2018-07-22 made omniwheel small started with form
    [Bearing MR 74 607_0.ipt, CycloidCurve.ipt, CycloidalGear.iam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]
2018-07-22 Have a choice of omniwheels
    [Drive.iam, DriveChain.iam, Form.ipt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]
2018-07-23 changed cycloid gear equations
    [Bom.xlsx, CycloidalGear.iam, Drive.iam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]
2018-07-24 Form got a threaded rod to move
    [BeltPulleyT5_12Z.ipt, Bom.xlsx, Drive.iam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]
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2018-07-26 Planetary Gear tolerance adaptions
    [PlanetGear.stl, PlanetaryGear.iam, PlanetaryGearConstr.iam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]
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2018-07-29 fixed Beltdrive files
    [BeltDriveConstruction.iam, Synchrone Riemenscheibe11.ipt, Synchrone Riemenscheibe21.ipt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]
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2018-07-31 2.nd try cycloid gear
    [CycloidalGear.iam, Enclosure.ipt, Enclosure2.ipt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]
2018-07-31 OmniWheel with 6mm bearings
    [BigRoll.stl, BottomCover.stl, CycloidalGear.iam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]
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2018-08-02 Start of BLDC code
    [BLDCController.kicad_pcb, BLDCController.sch]
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2018-08-05 blindly coded new controller with encoder
    [BeltDrive.iam, BeltDriveConstruction.iam, Bom.xlsx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]
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2018-08-10 new BLDC driver implementation turns
    [BeltDriveAxis.ipt, BeltDriveTest.iam, BushBeltDriveBR.ipt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]
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2018-08-14 Made Beltdriver tighter and adapted omniwheel to 2x5x2 bearings
    [BeltDrive.iam, BeltDriveTestHolder.ipt, BigRoll.stl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]
2018-08-18 beltdrive wheels got a flange
    [BeltDrive.iam, BeltDriveTestHolder.ipt, Drive.iam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]
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2018-08-19 updated drotek and pololu library
    [Bom.xlsx, MotorController.brd, MotorController.sch]
2018-08-19 removed flanges of wheels again
    [BeltDrive.iam, BushBeltDriveTL.ipt, DriveChain.iam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]
2018-08-20 constant distance from belt to enclosure
    [BeltDrive.iam, Drive.iam, DriveChain.iam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]
2018-08-26 Motor too weak and gets too hot. Mist.
    [Drive.iam, DriveChainDC.iam, EncoderEnclosure.ipt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]
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2018-08-29 read a lot of stuff about brushless motors
    [BeltDrive.iam, BeltDriveConstruction.iam, BeltDriveTestBed.iam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]
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2018-08-30 implemented self-tuning fuzzy PID controller
    [BeltGear.iam, BeltGear.ipt, Construction.iam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]
2018-09-01 made pulleys a tommy to let them centre theirselves
    [BeltGear.ipt, DriveChainEnclosure.ipt, Input.ipt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]
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2018-09-02 gave belt bearing bigger bearings
    [BeltGear.iam, BeltGear.ipt, Drive.iam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]
2018-09-05 First print of bottom sphere
    [AST_Bearings_SMR74.ipt, AST_Bearings_SMR74.stp, AST_Bearings_SMR74ZZ.ipt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]
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2018-09-16 Weekend before Monday print
    [Bauteil7.ipt, BeltGear.iam, BeltGear.ipt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]
2018-09-19 up to body print
    [Body.stl, ControllerPCBHolder.ipt, Drive.iam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]
2018-09-22 assembled engine and trying out new pcb
    [BeltDriveAxis.ipt, Bush-2mm.ipt, BushBeltDriveTL.ipt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]
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2018-10-04 i2c between webserver and bot controller
    [MotorController V2.brd, MotorController V2.sch]
2018-10-04 board now with ESP8266
    [MotorController V2.brd, MotorController V2.sch]
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2018-10-05 made motor more stiff in position control
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2018-10-10 added null value in IMU
    [ControllerPCBHolder.ipt, Drive.iam, DriveChain.iam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]
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2018-10-20 ESP8266 NodeMCU V2 foot print corrected
    [MotorController V3.brd, MotorController V3.sch]
2018-10-20 calibrated PID of lifter motor
    [MotorController V3.brd, MotorController V3.sch]
2018-10-20 PCB Holder correction(Teensy USB blocked was blocked by holder)
    [BeltGear.iam, ControllerPCBHolder.ipt, Drive.iam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]
2018-10-22 adapted PCB Holder to not have legs right at the USB port
    [ControllerPCBHolder.ipt, Drive.iam, PCBHolder.stl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]
2018-10-27 more aggressive Motor PID
    [MotorController V3.brd, MotorController V3.sch]
2018-10-27 bugfix: torque reduction after friction has been overcome should happens once only
    [BrushlessMotorDriver.cpp]
2018-10-27 aligned coord systems of IMU and kinematics
    [MotorController V3.brd, controller.xlsx]
2018-10-27 bugfix in log output
    [BallDrive.cpp]
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2018-11-07 heavy rewriting after first balancing trials
    [AS5047D.ipt, AS5047DEnclosure.ipt, BeltGear.iam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]
2018-11-10 does not yet balance
    [AS5047DEnclosure.ipt]
2018-11-14 Started V3 of Enclosure
    [BeltGear.iam, BushOmniWheel.ipt, Drive V2.iam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]
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2018-11-18 Replaced optical encoder by magnetic absolute encoders
    [AS5047DEnclosure.ipt]
2018-11-21 Worm gear for leg
    [BevelGear.iam, Drive V3.iam, DriveChain V3.iam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]
2018-11-24 almost ready to print
    [BevelGear.iam, ControllerPCBHolder.ipt, Drive V3.iam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]
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2018-11-28 Made PCB scaffold fit into barrel
    [BeltGear.iam, BeltGear.ipt, BodyConnector1.stl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]
2018-11-28 added switch in body's hat
    [Barrel.stl, BeltDriveAxisSleeve.stl, BodyTop.iam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]
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2018-12-01 Bugfix: magnetic field fixed for negative angles
    [AS5047D.cpp, BallDrive.cpp, BotController.cpp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]
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2018-12-03 Ordered PCB by Aisler!
    [MotorController V3.brd]
2018-12-08 Bugfix in angle computation of IMU
    [IMU.cpp, IMU.h, setup.h]
2018-12-09 balancing at 0 set point works, but disturbances are not yet compensated
    [Drive V3.iam, DriveChain V3.iam, DriveChainEnclosure V3.ipt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]
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2018-12-22 IMU failure
    [Drive V3.iam, DriveChain V3.iam, DriveChainEnclosure V3.ipt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]
2019-01-05 Body has a planetary gear now
    [DriveChain V4.iam, DriveChainEnclosure V4.ipt, GearAxisSleeve.ipt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]
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2019-01-08 made sun hole in planetary gear bigger and space between motorholder and planets
    [Barrel.stl, Bottom.ipt, Bottom.stl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]
2019-01-09 Model Simplification on planetary gear layer
    [25D Gearmotor Unit.iam, Bottom.ipt, Drive V4.iam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]
2019-01-11 Motorholder got tighter, Planetary Sun got 0.2 more play
    [Bottom.ipt, Bottom.stl, Drive V4.iam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]
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2019-01-20 First assembly of planetary gears
    [AS5047DEnclosure.stl, AS5047DEnclosureV2.ipt, Drive V4.iam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]

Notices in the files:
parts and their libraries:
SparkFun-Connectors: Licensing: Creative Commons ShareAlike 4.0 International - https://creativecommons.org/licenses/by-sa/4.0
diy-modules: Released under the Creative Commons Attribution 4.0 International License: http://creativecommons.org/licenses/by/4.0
